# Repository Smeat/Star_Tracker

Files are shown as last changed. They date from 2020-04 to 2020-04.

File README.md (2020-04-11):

# Goals of this fork
 * Add support for esp32
 * Use an sdmmc driver and be able to use a larger library
   * SIMBAD library for Vmag <11 is about 16mb for the data and 30mb for the names
 * Use a nokia 5110 LCD with red backlight LEDs
 * Visual representation on the screen
 * WiFi connection to KStars/Stellarium -> done with LX200
 * ESP32 support only for now (8bit support may return once the esp32 is running)
# Arduino Star Tracker

This project aims an **automatic control for telescopes**, is **based on Arduino** and is **low-cost**!

The control utilizes a calibration method and various settings which enable you to control **any type of mount** (not just equatorial and altazimuthal) pointed at any direction.

The **total cost** of upgrading your mount should be around **75 USD** (*SkyWatcher SynScan GOTO Upgrade for EQ3-2* costs around *460 USD*).

## Features

See [future work](#future-work) for missing features (like communication via USB or Bluetooth). Some implemented and working freatures:

* **Manual control** with various precision (degrees, arc minutes and arc seconds).
* **Automatic pointing** at predefined coordinates.
* Onboard **catalogue of deep sky objects** (the one which is present in Stellarium), so you can search thousands of Messier, Caldwell and NGC objects.
* Precise **tracking** (for any type of mount).
* **Parking** to default position.
* **Calibration** of **mount pole** which works similarly to All-Star polar alignement.
* **Camera control** which alows you to take photos with predefined exposure time and with a predefined period.
* **Wireless control** via IR remote control.
* Real **asynchronous** control of **stepper motors** (any other code can be run in parallel). 
* **LX200** support

## Hardware setup

#### 0. What you will need:
* **Arduino MEGA2560**, unfortunately Arduino Uno cannot be used due to the lack of memory
* **Power supply** or battery, e.g. *12V* and around *2.5A* (depends on your stepper motors)
* *2×* **NEMA 17** stepper motor (forget about 28BYJ!)
* *2×* stepper motor driver like **A4988**
* *2×* stepper driver **extender for A4988** (we will modify this part, so you should consider custom design with 100μF capacitor)
* *4×* **4k7** or **10k resistor** (or any other suitable resistor you hold in your hands)
* *(optionally)* **Gearboxes** for the motors (battery screwdriver is typically much cheaper than profi gearboxes and has some planetary gearboxes inside!)
* *2×* **flexible shaft couplers** for joing the motors with mount
* **Real Time Clock**, note that *DS3231* or more precise clocks are preffered over DS1307 
* **microSD Card module**
* **16×2 LCD** (without I2C module)
* **10k Potentiometer**
* **IR receiver**
* **Remote control**, you can use your favourite one you use for TV or you can use any other for makers! This repo settings match with a [remote control](https://www.makeblock.com/project/me-ir-remote-controller) by Makeblock. 
* Some kind of **transistor**, e. g. *BC337* and suitable resistor, e. g. *1k ohms* 
* **Bunch of wires and connectors**

#### 1. Parts modification and tuning

You should **add** the four **resistors** between `STEP`-`GND` and `DIR`-`GND` pins **to avoid a jitter** of stepper motors at startup. 

A typical extender for A4988 has an `ENABLE` pin, however, we do not need it. Instead, we **need a pin for controlling microstepping**. That is why you should hardwire the three microstepping pins and you should add a single pin to control them. Search for *microstepping resolution truth table* of A4988.

A **cheap IR remote control** might have a **weak diode**. In that case, you won't be able to control the mount from a distant places. So I recommend you to **replace the diode with a better one.**  

You also need to **tune potentiometers of stepper drivers**. Search for *How to set output current limit on A4988 stepper driver*. This can reduce noise produced by the motors or you can remove **problems with skipping of steps**. 

Use the **potentiometer** connected to the LCD to **adjust contrast**.

#### 2. Wiring

Wiring diagram

## Software Settings & Uploding to Arduino

#### 0. Prepearing libraries

The following list contains libraries you will need to sucessfuly compile the Star Tracker project (most of them is included in the Arduino IDE by default):

* [RTCLib](https://github.com/adafruit/RTClib)
* [LiquidCrystal](https://github.com/arduino-libraries/LiquidCrystal)
* [SD](https://github.com/arduino-libraries/SD)
* [SPI](https://www.arduino.cc/en/Reference/SPI)
* [Wire](https://www.arduino.cc/en/Reference/Wire)
* [EEPROM](https://www.arduino.cc/en/Reference/EEPROM)

At first, **make sure you have already installed all the libraries**.

#### 1. General configuration

Next, you should **modify** the `src/config.h` file to fit your needs. Familiarize yourself with all the definitions in the file. You should **definitely change** `LONGITUDE`, `LATITUDE`, `REDUCTION_RATIO_xx` and `DEG_PER_MOUNT_REV_xx` variables! You also need to change `DEFAULT_POLE_xx` if you use an altazimuthal mount.

You may encounter a problem with **stucked motors**. In that case, I advice you to **adjust** `ACCEL_STEPS_xx`, `ACCEL_DELAY_xx`, `FAST_DELAY_START_xx` and `FAST_DELAY_END_xx`. Change these definitions in order to change motors speed or ac/deceleration.

#### 2. Remote control

You need to **change definitions of key codes** to fit the protocol used by your favourite remote control. Take look **at the beginning** of the `src/keypad.h` file. There are few definitions of `KP_KEY_xx` where `xx` describes the particular key. To figure out **codes used by your remote control**, upload the following sketch to your Arduino:

```
#include <Arduino.h>
#include <IRremote.h>
#include "src/config.h"

IRrecv ir(KEYPAD_IR_PIN);
decode_results results;

void setup(){
    Serial.begin(9600);
    ir.enableIRIn();
}

void loop(){
    if (!ir.decode(&results)) {
      delay(5);
      return;
    }
    Serial.println(results.value, HEX);
    ir.resume();
    delay(500);
}
```

Then **open the Serial monitor** and **observe the key codes** of pressed keys. Note that you will receive `0xFFFFFFFF` when you hold a key continuously.

You can also **change mapping of these keys to particular actions** in the `src/control.h` file (but be careful as these keys and actions should not cause conflicts and ambiguity).

#### 3. SD card and catalogue

Take an **empty and formatted microSD** card and **copy there the content** of the `SD` directory. It should be a single file `catalog.csv` which is a limited version of **Stellarium catalogue of deep space objects**. You can delete or add object to this file, however the structure and meaning of columns should be preserved.

#### 4. Real Time Clock

The `src/rtc_ds3231.h` file contains implementation of `Clock` class for `DS3231` module. In case you use **other module** or you want to obtain time from NTP servers, **implement** the `Clock` interface and change some lines in `Star_Tracker.ino`.

#### 5. Camera trigger

Similarly, you may need to change the implementation of the camera trigger control. The `src/CanonEOS1000D.h` file contains implementation of `CameraController` class for *Canon EOS1000D*. If you have other camera with **other trigger logic**, you should **create a new implementation** of `CameraController` and change some lines at `Star_Tracker.ino`. Note that in this case, you may also need a different wiring!

## Notes on precision

The only loss of precision is caused by Arduino's floating point unit which cannot work with 64-bit floating point numbers. Especially while computing extremal values of some goniometric funcions (tangens and other functions which are reduced to computing tangens). These problems can occur while pointing to stars near celestial pole. The GoTo feature can miss few arc minutes and alignement can be imprecise in that case. However points with lower DEC values should be handled properly.  

The tracking with very badly aligned mount can also be imprecise after some time because the speeds of DEC and RA motors are computed just once at the start of the movement. Unfortunately these speeds does not have to be constant necessarily.

## Future work

- [ ] enable **serial communication** with *USB* and *Bluetooth*
- [ ]  better **speed** computation **while tracking**
- [ ]  compute **alignment analytically**

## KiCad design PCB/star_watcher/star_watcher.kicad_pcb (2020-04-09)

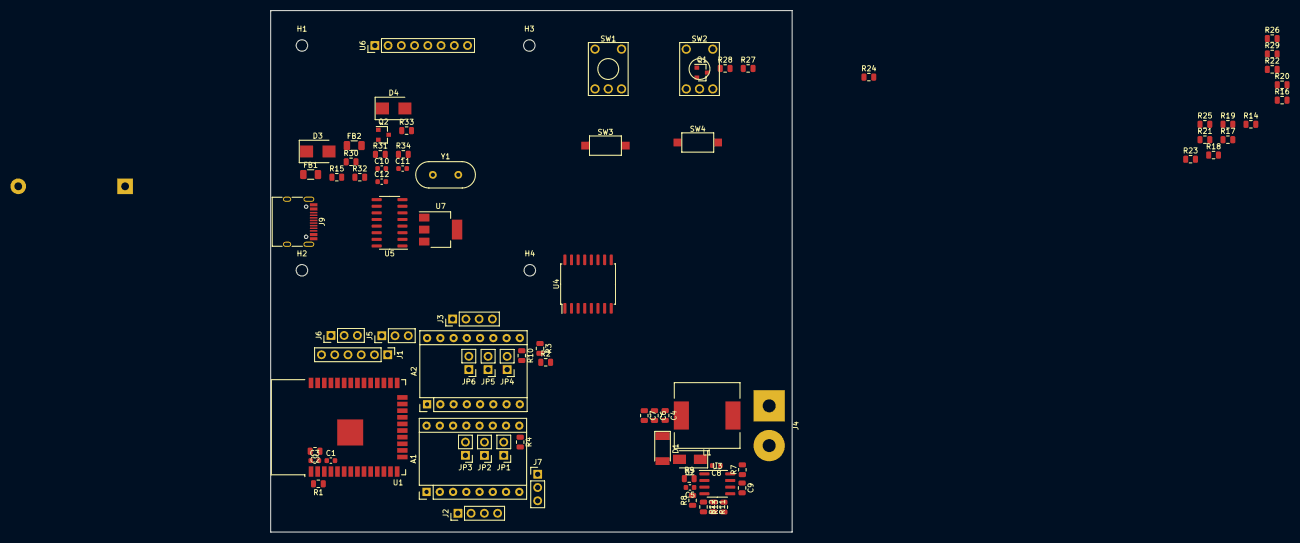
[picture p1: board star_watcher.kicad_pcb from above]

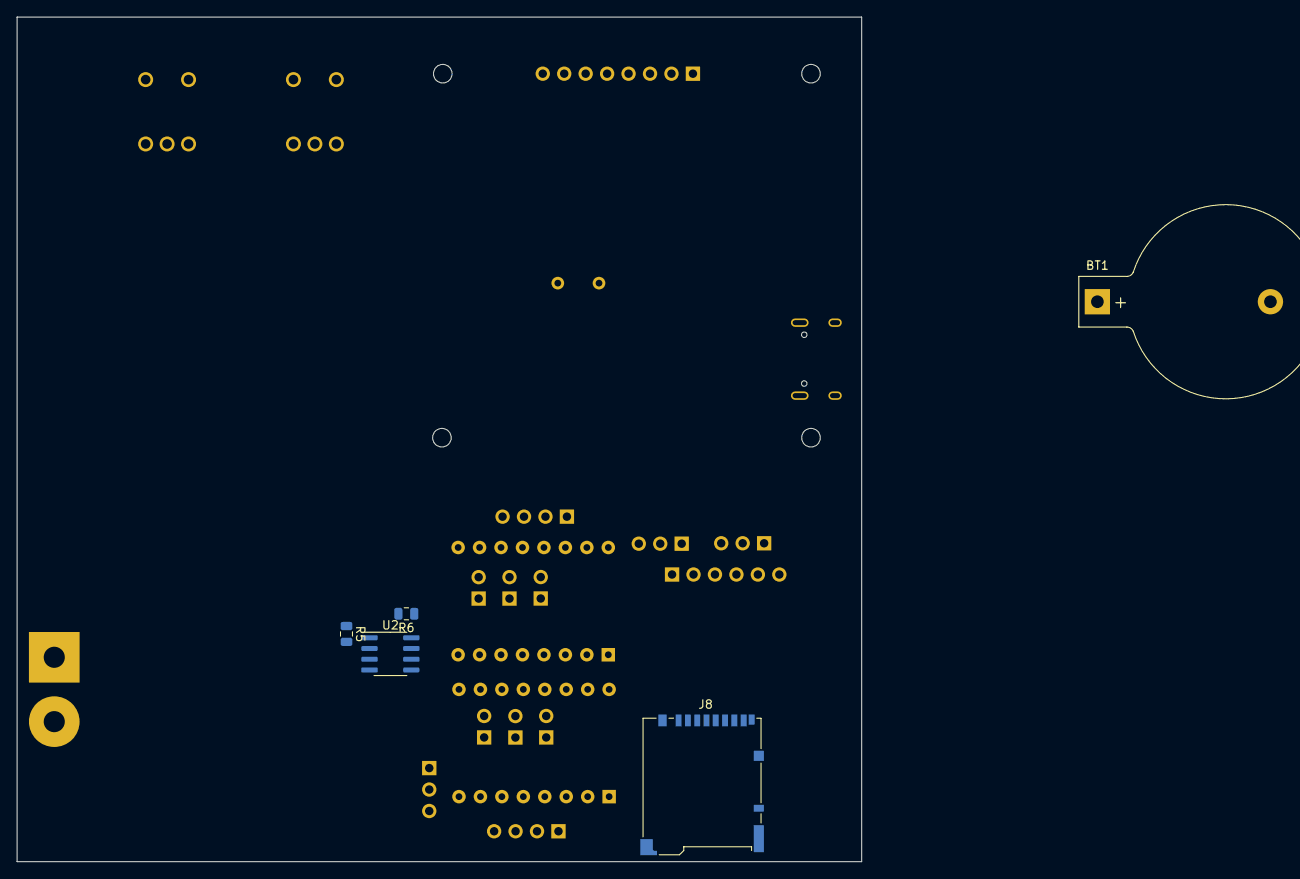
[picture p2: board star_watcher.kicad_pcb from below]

Board: 2 copper layers, 100.0 x 100.0 mm, 89 parts (5 on the bottom side), 78 nets, no tracks yet.

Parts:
A1, A2: Pololu_Breakout_A4988; Pololu_Breakout-16_15.2x20.3mm
BT1: Battery_Cell; BatteryHolder_Keystone_103_1x20mm
C1, C3, C8, C10: 0.1µF; C_0603_1608Metric
C2, C4, C6, C7, C9: 10µF; C_0805_2012Metric
C5: 150pF; C_0603_1608Metric
C11, C12: C; C_0603_1608Metric
D1: 3.5; D_MELF
D2: D_Schottky; D_SMA
D3, D4: D_TVS; D_SMB
FB1, FB2: Ferrite_Bead; L_1206_3216Metric
H1, H2, H3, H4: MountingHole; MountingHole_2.2mm_M2
J1: Programming; PinHeader_1x06_P2.54mm_Vertical
J2: Motor2; PinHeader_1x04_P2.54mm_Vertical
J3: Motor1; PinHeader_1x04_P2.54mm_Vertical
J4: input power; SolderWirePad_1x02_P7.62mm_Drill2.5mm
J5: UART1; PinHeader_1x03_P2.54mm_Vertical
J6: UART2; PinHeader_1x03_P2.54mm_Vertical
J7: I2C; PinHeader_1x03_P2.54mm_Vertical
J8: Micro_SD_Card_Det; microSD_HC_Hirose_DM3BT-DSF-PEJS
J9: USB_C_Receptacle_USB2.0; USB_C_Receptacle_HRO_TYPE-C-31-M-12
JP1, JP2, JP3, JP4, JP5, JP6: Jumper; PinHeader_1x02_P2.54mm_Vertical
L1: 22µH; L_12x12mm_H6mm
Q1, Q2: Q_PMOS_DGS; SOT-23
R1, R3, R4, R5, R6, R17, R18, R19, R20, R21, R22, R23, R24, R25, R26, R27, R28, R29: 10k; R_0805_2012Metric
R2: 240k; R_0805_2012Metric
R7, R8, R10: 100k; R_0805_2012Metric
R9: 59k; R_0805_2012Metric
R11, R14, R15, R16, R30, R31, R32, R33, R34: R; R_0805_2012Metric
R12: 40.2k; R_0805_2012Metric
R13: 200k; R_0805_2012Metric
SW1, SW2: Rotary_Encoder_Switch; KSA_Tactile_SPST
SW3, SW4: SW_Push; SW_SPST_CK_RS282G05A3
U1: ESP32-WROOM-32U; ESP32-WROOM-32
U2: DS3231MZ; SOIC-8_3.9x4.9mm_P1.27mm
U3: MP1584; SOIC-8_3.9x4.9mm_P1.27mm
U4: PCF8574; SOIC-16W_7.5x10.3mm_P1.27mm
U5: CH340G; SOIC-16_3.9x9.9mm_P1.27mm
U6: 5110; PinHeader_1x08_P2.54mm_Vertical
U7: AMS1117; SOT-223
Y1: 12MHz; Crystal_HC49-4H_Vertical

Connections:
+3V3: A1.2, A2.2, C2.1, C3.2, C4.2, C6.2, C7.2, D1.1, J1.2, J8.4, JP1.1, JP2.1, JP3.1, JP4.1, JP5.1, JP6.1, L1.2, Q1.3, Q2.3, R1.2, R4.2, R5.1, R6.1, R10.2, R11.2, R14.1, R17.1, R18.1, R19.1, R20.1, R21.1, R22.1, R23.2, R24.2, R25.1, R26.1, R27.1, R28.1, R29.1, U1.2, U2.2, U4.16, U5.4, U5.16, U6.6
+28V: A1.8, A2.8, C9.1, J4.1, Q2.2, R2.2, R7.1, R34.1, U3.7
/3.3V_USB: Q2.1, R32.1, U7.2, U7.4
/CE_5110: U1.27, U6.2
/DC_5110: U1.29, U6.3
/DIR1: A2.16, U1.28
/DIR2: A1.16, U1.31
/DTR: J1.3, SW4.1, U1.25, U5.13
/EN1: A2.9, R10.1
/EN2: A1.9, R4.1
/LCD_BACKLIGHT: Q1.2, U1.11
/PUSH1: R14.2, SW3.1, U1.5
/ROTARY1_A: R24.1, SW1.5, U4.7
/ROTARY1_B: R26.2, SW1.3, U4.9
/ROTARY1_PUSH: R27.2, SW1.1, U4.5
/ROTARY2_A: R23.1, SW2.5, U4.6
/ROTARY2_B: R25.2, SW2.3, U4.10
/ROTARY2_PUSH: R28.2, SW2.1, U4.4
/RST_5110: R29.2, U4.11, U6.1
/RTC_RST: U2.4, U4.12
/RTS: C1.1, J1.4, R1.1, U1.3, U5.14
/RX0: J1.5, U1.34, U5.2
/RX1: J5.2, U1.7
/RX2: J6.2, U1.6
/SCL: J7.2, R6.2, U1.37, U2.8, U4.14
/SDA: J7.1, R5.2, U1.36, U2.7, U4.15
/SD_CLK: J8.5, R21.2, U1.13
/SD_CMD: J8.3, R22.2, U1.23
/SD_D0: J8.7, R17.2, U1.24
/SD_D1: J8.8, R18.2, U1.26
/SD_D2: J8.1, R20.2, U1.14
/SD_D3: J8.2, R19.2, U1.16
/SPI_MOSI: U1.9, U6.4
/SPI_SCK: U1.8, U6.5
/STEP1: A2.15, U1.30
/STEP2: A1.15, U1.33
/TX0: J1.6, U1.35, U5.3
/TX1: J5.1, U1.10
/TX2: J6.1, U1.12
/USB_D+: D3.1, J9.A6, J9.B6, U5.5
/USB_D-: D4.2, J9.A7, J9.B7, U5.6
/VBUS: FB2.1, U7.3
/V_BAT_SENSE: R2.1, R3.2, U1.4
GND: A1.1, A1.7, A2.1, A2.7, BT1.2, C1.2, C2.2, C3.1, C4.1, C6.1, C7.1, C9.2, C10.1, C11.2, C12.2, D1.2, D2.2, D3.2, D4.1, FB1.2, J1.1, J4.2, J5.3, J6.3, J7.3, J8.6, J8.11, R3.1, R8.1, R9.1, R12.2, R13.1, R15.2, R30.1, R31.1, R33.2, R34.2, SW1.2, SW1.4, SW2.2, SW2.4, SW3.2, SW4.2, U1.1, U1.15, U1.38, U1.39, U2.5, U3.5, U4.1, U4.2, U4.3, U4.8, U5.1, U6.8
unnamed: A1.3, J2.1
unnamed: A1.4, J2.2
unnamed: A1.5, J2.3
unnamed: A1.6, J2.4
unnamed: A1.10, JP1.2
unnamed: A1.11, JP2.2
unnamed: A1.12, JP3.2
unnamed: A1.13, A1.14
unnamed: A2.3, J3.1
unnamed: A2.4, J3.2
unnamed: A2.5, J3.3
unnamed: A2.6, J3.4
unnamed: A2.10, JP4.2
unnamed: A2.11, JP5.2
unnamed: A2.12, JP6.2
unnamed: A2.13, A2.14
unnamed: BT1.1, U2.6
unnamed: C5.1, U3.3
unnamed: C5.2, R8.2
unnamed: C8.1, U3.8
unnamed: C8.2, D2.1, L1.1, U3.1
unnamed: C10.2, J9.S1, R15.1
unnamed: C11.1, U5.7, Y1.1
unnamed: C12.1, U5.8, Y1.2
unnamed: FB1.1, J9.A1, J9.A12, J9.B1, J9.B12
unnamed: FB2.2, J9.A4, J9.A9, J9.B4, J9.B9
unnamed: J9.A5, R30.2
unnamed: J9.B5, R31.2
unnamed: Q1.1, R16.2
unnamed: R7.2, R9.2, U3.2
unnamed: R11.1, R12.1, U3.4
unnamed: R13.2, U3.6
unnamed: R16.1, U6.7
unnamed: R32.2, R33.1, U7.1

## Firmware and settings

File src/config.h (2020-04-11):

#ifndef CONFIG_H
#define CONFIG_H

/* ================================== GENERAL SETTINGS ================================== */

#define SERIAL_BAUD_RATE       115200
#define EEPROM_ADDR            0            // starting EEPROM offset, 18 bytes needed 
#define VERSION                1.0

#define LONGITUDE              16.2607719   // CHANGE THIS !!!!!
#define LATITUDE               49.8225003   // CHANGE THIS !!!!!


/* ======================================== MOUNT ======================================= */

#define REDUCTION_RATIO_DEC     1              // reduction ratio of DEC motor gearbox (1:8)
#define REDUCTION_RATIO_RA      1              // reduction ratio of RA motor gearbox (1:8)
#define DEG_PER_MOUNT_REV_DEC   1 // reduction ratio of DEC mount gears (1:67)
#define DEG_PER_MOUNT_REV_RA    1  // reduction ratio of DEC mount gears (1:134)

#define DIRECTION_DEC           0    // 1 or 0 to swap DEC movement direction
#define DIRECTION_RA            0    // 1 or 0 to swap RA movement direction

#define DEFAULT_POLE_RA         0    // default equatorial coordinates of the mount pole 
#define DEFAULT_POLE_DEC        5   // these values are changed during alignment
#define DEFUALT_RA_OFFSET       0    // offset of RA axis (defines where mount's local RA is 0)


// Alignement is done by optimization of rotation matrix parameters (three), this is done 
// by a simple evolutionary strategy. Exact numeric solutions can be unstable due to Arduino
// doubleing point precision and I haven't found a better soluiton than this :( 

#define CAL_BUFFER_SIZE         12         // maximal number of point pairs used for alignmenet
#define OPT_PRECISION           5000000    // if objective is less then 1/OPT_PRECISION, opt. stops
#define OPT_POPULATION_SIZE     4          // population size of the ES
#define OPT_GENERAITONS         1250       // # gen., reduce for faster but less precise solutions
                                           // higher number of generations probably does not imply
                                           // better solutions
#define OPT_SIGMA               1.0        // initial sigma value
#define OPT_SIGMA_DECAY         0.997      // every generation is sigma multiplied by this value 


/* ==================================== STEPPER MOTORS ================================== */

#ifdef BOARD_ATMEGA
#define MOTORS_PORT             PORTK  // port of pins of stepper motors (serach for A. Mega pinout)
#define MOTORS_DDR              DDRK   // DDR of pins of stepper motors
#define STEP_PIN_DEC            PK2    // = A8 
#define DIR_PIN_DEC             PK1    // = A9
#define MS_PIN_DEC              PK0    // = A10
#define STEP_PIN_RA             PK5    // = A13
#define DIR_PIN_RA              PK4    // = A12
#define MS_PIN_RA               PK3    // = A11
#else
#define STEP_PIN_DEC            21    // = A8 
#define DIR_PIN_DEC             17    // = A9
#define MS_PIN_DEC              13    // = A10
#define STEP_PIN_RA             14    // = A13
#define DIR_PIN_RA              25    // = A12
#define MS_PIN_RA               22    // = A11
#endif

#define MICROSTEPPING_MUL       1   // level of microstepping (depends of your wiring of A4988 pins)

#define STEPS_PER_REV_DEC       (16*200)     // number of steps per DEC motor revolution (200 for NEMA 17)
#define STEPS_PER_REV_RA        (16*200)     // number of steps per RA motor revolution (200 for NEMA 17)

// period in µs
#define TMR_RESOLUTION  64

#define ACCEL_STEPS_DEC         256     // every ACCEL_STEPS_DEC steps is the delay in/decreased by
#define ACCEL_DELAY_DEC         64      // ACCEL_DELAY_DEC (should be even, multiple of 2)
#define FAST_DELAY_START_DEC    2048    // DEC delay at the start of fast movement (2048 us, ~488 Hz)
#define FAST_DELAY_END_DEC      0    // DEC delay at the end of fast movement (1024 us, ~976 Hz)

#define ACCEL_STEPS_RA          256     // every ACCEL_STEPS_RA steps is the delay in/decreased by
#define ACCEL_DELAY_RA          64      // ACCEL_DELAY_RA (should be even, multiple of 2)
#define FAST_DELAY_START_RA     2048    // RA delay at the start of fast movement (2048 us, ~488 Hz)
#define FAST_DELAY_END_RA       0    // RA delay at the end of fast movement (1024 us, ~976 Hz)

#define FAST_REVS_PER_SEC_DEC   1000000.0 / FAST_DELAY_START_DEC / STEPS_PER_REV_DEC 
#define FAST_REVS_PER_SEC_RA    1000000.0 / FAST_DELAY_START_RA  / STEPS_PER_REV_RA


/* ==================================== OTHER SETTINGS ================================== */

#define TRIGGER_PIN             40      // pin which controls camera trigger
#define SNAP_DELAY_MS           2000    // minimal delay (ms) between two snaps (camera protection)

#define SD_CS                   53      // SD card chip select pin

#define KEYPAD_IR_PIN           7       // IR receiver signal pin 
#define SHORT_HOLD_TIME_MS      200     // minimal duration (ms) of a fast remote control key press
#define LONG_HOLD_TIME_MS       800     // minimal duration (ms) of a slow remote control key press

#define DSP_DATA_PIN4           2       // LCD data pins
#define DSP_DATA_PIN5           3
#define DSP_DATA_PIN6           4
#define DSP_DATA_PIN7           5
#define DSP_ANODE_PIN           8       // LCD pin for controling brightness
#define DSP_ENABLE_PIN          11      // LCD enable pin
#define DSP_REGISTER_SEL_PIN    12      // LCD register select pin

/* ======================================== DEBUG_OUTPUT ======================================= */

// #define DEBUG_OUTPUT
// #define DEBUG_OUTPUT_MOUNT
// #define DEBUG_OUTPUT_TIME
// #define DEBUG_OUTPUT_CONTROL
// #define DEBUG_OUTPUT_KEYS

#endif

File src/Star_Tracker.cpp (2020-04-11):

#include "esp_attr.h"
#include "freertos/portmacro.h"
#include "freertos/projdefs.h"
#define LOG_LOCAL_LEVEL ESP_LOG_VERBOSE
#include "config.h"
#include "control/control.h"
#include "control/LX200.h"

#include "core/motor_controller.h"
#include "core/mount_controller.h"

#include "core/camera_controller.h"
#include "core/canon_eos1000d.h"

#include "core/clock.h"
#include "core/rtc_ds3231.h"

#include "net/TCP.h"
#include "net/wireless.h"

#include <stdint.h>
#include <soc/timer_group_struct.h>
#include <soc/timer_group_reg.h>
#include <esp_task_wdt.h>

RtcDS3231 ds3231;
Clock& my_clock = ds3231;

CanonEOS1000D eos;
CameraController& camera = eos; 

MountController mount(MotorController::instance());

Control control(mount, camera, my_clock);

void watchdog_feed() {
  TIMERG0.wdt_wprotect = TIMG_WDT_WKEY_VALUE;
  TIMERG0.wdt_feed = 1;
  TIMERG0.wdt_wprotect = 0;
}

void watchdog_add_task() {
	esp_task_wdt_add(NULL);
}

void tcp_task(void* param) {
	while(42) {
  		control.update();
  		tcp_update(lx200_handle_message);
		//uint8_t buf[] = ":Sr 10:10:10#";
//		lx200_handle_message(buf, strlen((char*)buf));
//		mount.set_target_dec(5);
//		mount.set_target_ra(5);
		vTaskDelay(10/portTICK_PERIOD_MS);
	}
}

void IRAM_ATTR motor_task(void* param) {
//	watchdog_add_task();
	uint8_t state = 0;
	while(42) {
		ulTaskNotifyTake(pdTRUE, portMAX_DELAY);
		digitalWrite(33, state);
		state = !state;
		MotorController::instance().trigger();
//		watchdog_feed();
	}
}

hw_timer_t* motor_timer = NULL;
static TaskHandle_t motor_task_handle = NULL;

void IRAM_ATTR motor_isr() {
	BaseType_t xHigherPriorityTaskWoken = pdFALSE;
	vTaskNotifyGiveFromISR(motor_task_handle, &xHigherPriorityTaskWoken);
	if(xHigherPriorityTaskWoken) {
		portYIELD_FROM_ISR();
	}
}

void info_task(void*) {
	while(42) {
//		mount.get_global_mount_orientation();

		log_v("Moving to 90,0");
		mount.move_absolute(90, 0);
		log_v("done!");
		// FIXME: timing problem. if delay is too small I don't reach the target
		// seems to be another problem
		do {
			log_v("Waiting for mount controller...");
			vTaskDelay(10000/portTICK_PERIOD_MS);
		} while(mount.is_moving());
		log_v("Moving to -20,0");
		mount.move_absolute(-20, 0);
		do {
			log_v("Waiting for mount controller...");
			vTaskDelay(10000/portTICK_PERIOD_MS);
		} while(mount.is_moving());
	}
}

void setup() {
	pinMode(33, OUTPUT);
  Serial.begin(SERIAL_BAUD_RATE);
  esp_log_level_set("*", ESP_LOG_VERBOSE);
  Serial.println("Starting tcp, lx200 and wifi");
  log_e("TEST!");
  ESP_LOGI("HI", "ESP test!");
  lx200_init(&mount, &my_clock);
  initWifiAP();
  tcp_init();
  delay(10);
  control.initialize();
  delay(100);

  xTaskCreatePinnedToCore(&tcp_task, "tcp_task", 18096, NULL, 5, NULL, 1);
//  xTaskCreatePinnedToCore(&info_task, "info_task", 8096, NULL, 5, NULL, 1);
  xTaskCreatePinnedToCore(&motor_task, "motor_task", 8096, NULL, 5, &motor_task_handle, 0);

  motor_timer = timerBegin(0, 80, true);
  timerAttachInterrupt(motor_timer, &motor_isr, true);
  timerAlarmWrite(motor_timer, TMR_RESOLUTION, true);
  timerAlarmEnable(motor_timer);

}

void loop() {
	mount.update_tracking();
	vTaskDelay(10/portTICK_PERIOD_MS);
//	watchdog_feed();
}

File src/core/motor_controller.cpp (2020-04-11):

#include "config.h"
#include "esp32-hal-gpio.h"
#include "freertos/portmacro.h"
#include "stdint.h"
#define FROM_LIB

#include <Arduino.h>
#include "esp32-hal-timer.h"
#include "motor_controller.h"

void MotorController::initialize() {
#ifdef BOARD_ATMEGA    
    uint8_t pin_mask = (1 << STEP_PIN_DEC) | (1 << DIR_PIN_DEC) | (1 << MS_PIN_DEC) |
                       (1 << STEP_PIN_RA)  | (1 << DIR_PIN_RA)  | (1 << MS_PIN_RA);

    MOTORS_DDR |= pin_mask;
    MOTORS_PORT &= ~pin_mask;

    #ifdef DEBUG_OUTPUT
        Serial.println(F("Stepper motors pins initialized:"));
        Serial.print(F("  Pinout: ")); Serial.println(pin_mask, BIN);
        Serial.print(F("  DDR:    ")); Serial.println(MOTORS_DDR, BIN);
        Serial.print(F("  PORT:   ")); Serial.println(MOTORS_PORT, BIN);
    #endif

    // Timer/Counter Control Register: set Fast PWM mode
    TCCR5A = 0x23 ; // || set mode 7 (Fast PWM) with
    TCCR5B = 0x09 ; // || prescaler 1 (no prescaling)

    // Output Compare Register: set interrupt frequency
    OCR5A = TIMER_TOP - 1;
    OCR5B = 0;
      
    // Timer/Counter Interrupt Mask Register: set interrupt TIMERx_COMPA_vect
    TIMSK5 |= (1 << OCIE5A);

    #ifdef DEBUG_OUTPUT
        Serial.println(F("TimerX initialized."));
        Serial.print(F("  TCCRxA: ")); Serial.println(TCCR5A, BIN);
        Serial.print(F("  TCCRxB: ")); Serial.println(TCCR5B, BIN);
        Serial.print(F("  TIMSKx: ")); Serial.println(TIMSK5, BIN);
    #endif
#else
	pinMode(STEP_PIN_DEC, OUTPUT);
	pinMode(DIR_PIN_DEC, OUTPUT);
	pinMode(MS_PIN_DEC, OUTPUT);
	pinMode(STEP_PIN_RA, OUTPUT);
	pinMode(DIR_PIN_RA, OUTPUT);
	pinMode(MS_PIN_RA, OUTPUT);

#endif

    _commands = queue<command_t>(8);

    _dec_balance = 0;
    _ra_balance = 0;
	_motor_lock = xSemaphoreCreateMutex();
}

void MotorController::stop() {

	xSemaphoreTake(_motor_lock, portMAX_DELAY);
    #ifdef DEBUG_OUTPUT
        Serial.println(F("Stopping both motors:"));
    #endif
    
    cli();
    _dec.pulses_remaining = 0;
    _ra.pulses_remaining = 0;
    sei();

    #ifdef DEBUG_OUTPUT
        Serial.print(F("  DEC: ")); Serial.println(_dec.pulses_remaining);
        Serial.print(F("  RA:  ")); Serial.println(_ra.pulses_remaining);
    #endif
      
#ifdef BOARD_ATMEGA
    MOTORS_PORT &= ~((1 << STEP_PIN_DEC) | (1 << STEP_PIN_RA)); // step pins to LOW

    #ifdef DEBUG_OUTPUT
        Serial.print(F("  PORT:   ")); Serial.println(MOTORS_PORT, BIN);
    #endif
#else
	digitalWrite(STEP_PIN_DEC, LOW);
	digitalWrite(STEP_PIN_RA, LOW);
#endif

    _commands.clear();
	xSemaphoreGive(_motor_lock);
}

double MotorController::estimate_fast_turn_time(double revs_dec, double revs_ra) {

    int sd, sr;
    revs_to_steps(&sd, &sr, revs_dec, revs_ra, false);
    
    auto time_dec = estimate_motor_fast_turn_time(sd, ACCEL_STEPS_DEC, ACCEL_DELAY_DEC, FAST_DELAY_START_DEC, FAST_DELAY_END_DEC);
    auto time_ra  = estimate_motor_fast_turn_time(sr, ACCEL_STEPS_RA,  ACCEL_DELAY_RA,  FAST_DELAY_START_RA,  FAST_DELAY_END_RA);

    return max(time_dec, time_ra);
} 

double MotorController::estimate_motor_fast_turn_time(double steps, int accel_each, int accel_amount, int delay_start, int delay_end) {

    double time = 0;

    double total_steps = floor(steps);
    double accel_steps = floor(steps);
    int delay_curr = delay_start; 

    for (accel_steps -= accel_each; (accel_steps > steps / 2.0) && (delay_curr > delay_end);) {
        time += (double)delay_curr * accel_each;
        delay_curr -= accel_amount;
        accel_steps -= accel_each;
    }
    accel_steps += accel_each;

    return (2 * time + (2 * accel_steps - total_steps) * delay_curr) / 1000.0; 
}

void MotorController::fast_turn(double revs_dec, double revs_ra, boolean queueing) {
    turn_internal({revs_dec, revs_ra, FAST_DELAY_START_DEC, FAST_DELAY_START_RA, FAST_DELAY_END_DEC, FAST_DELAY_END_RA, false}, queueing);
}

void MotorController::slow_turn(double revs_dec, double revs_ra, double speed_dec, double speed_ra, boolean queueing) {
    // revolutions per second convert to delay in micros
    // there might be some overflows, but nobody cares ... (hopefully)
    uint32_t delay_dec = 1000000.0 / (speed_dec * STEPS_PER_REV_DEC * MICROSTEPPING_MUL);
    uint32_t delay_ra  = 1000000.0 / (speed_ra  * STEPS_PER_REV_RA  * MICROSTEPPING_MUL);
    turn_internal({revs_dec, revs_ra, delay_dec, delay_ra, delay_dec, delay_ra, true}, queueing);
}

void MotorController::turn_internal(command_t cmd, bool queueing) {
    if (queueing && !is_ready()) {
        _commands.push(cmd);
        return;
    }
	xSemaphoreTake(_motor_lock, portMAX_DELAY);
    int steps_dec, steps_ra;
    revs_to_steps(&steps_dec, &steps_ra, cmd.revs_dec, cmd.revs_ra, cmd.microstepping);
	log_d("turning by DEC %f RA %f revs, %d %d steps %d %d balance",cmd.revs_dec, cmd.revs_ra, steps_dec, steps_ra, this->_dec_balance, this->_ra_balance);
	log_d("total steps ra %d dec %d", _dec_balance, _ra_balance);
	
    //cli();

    // wait 1ms for pins to stabilize if needed
    bool dec_rev = cmd.revs_dec < 0;
	bool ra_rev = cmd.revs_ra < 0;


    int32_t effective_steps_dec = steps_dec;
    int32_t effective_steps_ra = steps_ra;

    _dec.pulses_to_accel = 0;
    _ra.pulses_to_accel  = 0;

    _dec.steps_total = effective_steps_dec;
    _ra.steps_total = effective_steps_ra;
    
    _dec.target_steps_delay = cmd.delay_end_dec;
    _ra.target_steps_delay  = cmd.delay_end_ra;

    _dec.start_steps_delay = cmd.delay_start_dec;
    _ra.start_steps_delay  = cmd.delay_start_ra;

    step_micros(&_dec, effective_steps_dec * 2, _dec.start_steps_delay, dec_rev);
    step_micros(&_ra,  effective_steps_ra  * 2, _ra.start_steps_delay, ra_rev);
        log_d("Initializing new movement.");
        log_d("  revs DEC:       %f", cmd.revs_dec);
        log_d("  resv RA:        %f", cmd.revs_ra);
		log_d("  steps DEC: %d RA: %d", effective_steps_dec, effective_steps_ra);
        log_d("  micro s. (t/f): %s", cmd.microstepping ? "enabled" : "disabled");
		log_d("Direction dec %d ra %d", digitalRead(DIR_PIN_DEC), digitalRead(DIR_PIN_RA));
	xSemaphoreGive(_motor_lock);

    // compensate coarse resolution of the full-step movement
    if (!cmd.microstepping) {
        double revs_dec, revs_ra;
        steps_to_revs(&revs_dec, &revs_ra, steps_dec - effective_steps_dec, steps_ra - effective_steps_ra, false);
        slow_turn(revs_dec, revs_ra, FAST_REVS_PER_SEC_DEC / MICROSTEPPING_MUL, FAST_REVS_PER_SEC_RA / MICROSTEPPING_MUL, true);
    }

#ifdef BOARD_ATMEGA
    TCNT1 = 0; // reset Timer1 counter
#endif

    //sei();
}

bool MotorController::change_pin(byte pin, byte value) {
#ifdef BOARD_ATMEGA
    if (((MOTORS_PORT >> pin) & 1) == value) return false;
    MOTORS_PORT ^= (-value ^ MOTORS_PORT) & (1 << pin);
#else
	uint8_t state = digitalRead(pin);
	if(state == value) return false;
	digitalWrite(pin, value);
	log_d("Changed pin %d to %d", pin, value);
#endif
    return true;
}
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

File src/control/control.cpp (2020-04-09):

#define FROM_LIB

#include "control.h"

void Control::initialize() {

    load(_shooting_time_buffer, EEPROM_ADDR, 1, 9999, 30);
    load(_shooting_delay_buffer, EEPROM_ADDR + 2, 1, 9999, 30);
    load(_brightness_buffer, EEPROM_ADDR + 4, 0, 255, 128);

    _mount.initialize();
	log_i("Mount init done");
    _display.initialize(_brightness_buffer);
	log_i("display init done");

#ifdef BOARD_ATMEGA
    SD.begin(SD_CS);
    _sd = &SD;
#endif
    _keypad.initialize();
	log_i("keypad init done");
    _camera.initialize();
	log_i("camera init done");

    _clock.obtain_time();
	log_i("clock init done");

    delay(100);

    _state = MAIN;
    _state_changed = true;
}

void Control::update() {

    _keypad.update();
    _camera.update();

    _last_state_changed = _state_changed;
    _last_substate_changed = _substate_changed;
    _state_changed = false;
    _substate_changed = false;

    if (_keypad.pressed(C_EXIT)) change_state(HELP);

    switch (_state) {
        case MAIN: 	  main_menu(); break;
        case HELP: 	  help_menu(); break;
        case GOTO: 	  goto_menu(); break;
        case CALIB:   calibration_menu(); break;
        case SHOOT:   camera_menu(); break;
        case CATALOG: catalogue_menu(); break;
        case TIME:    time_menu(); break;
        case BRIGHT:    brightness_menu(); break;
        case POSITION:  position_menu(); break;
    }
}

void Control::help_menu() {

    if (_last_state_changed) _last_substate_change_time = millis();

    if (_keypad.pushed(C_EXIT)) change_state(MAIN);

    if ((millis() - _last_substate_change_time) > INFO_SCREEN_MS) {
        _last_substate_change_time = millis();
        change_substate(increment_substate());
        if (_substate > S9) change_substate(S0);
    }

    _display.render_help(_last_state_changed || _last_substate_changed, _substate);			
}

void Control::position_menu() {

    if (_keypad.pushed(C_EXIT)) change_state(MAIN);

    auto orientation = _mount.get_global_mount_orientation();
    _display.render_position(_last_state_changed || _last_substate_changed, orientation.ra, orientation.dec);			
}

void Control::brightness_menu() {

    if (_keypad.pushed(C_EXIT)) {
        change_state(MAIN);
        save(_brightness_buffer, EEPROM_ADDR + 4);
    }

    int change = 0;
    if (_keypad.pressed(C_ARROW_UP))    	change = 32;
    else if (_keypad.pressed(C_ARROW_DOWN)) change = -32;	
    else if (_keypad.pushed(C_ARROW_UP))    change = 8;
    else if (_keypad.pushed(C_ARROW_DOWN))  change = -8;

    _brightness_buffer += change;
    if (_brightness_buffer > 255) _brightness_buffer = 255;
    if (_brightness_buffer < 0) _brightness_buffer = 0;

    _display.render_brightness(_last_state_changed, _brightness_buffer, change != 0);
    _display.set_brightness(_brightness_buffer);
}

void Control::main_menu() {

    if (_keypad.pressed(C_TRACKING))     	_mount.set_tracking();
    else if (_keypad.pushed(C_GOTO))     	change_state(GOTO);
    else if (_keypad.pushed(C_POSITION)) 	change_state(POSITION);
    else if (_keypad.pushed(C_PARKING)) {
        _camera.reset();
        _mount.stop_all();
        _mount.set_parking();
    }
    else if (_keypad.pushed(C_BRIGHTNESS))  change_state(BRIGHT);	
    else if (_keypad.pushed(C_SHOOT))       _camera.shoot(_shooting_time_buffer, _shooting_delay_buffer);
    else if (_keypad.pressed(C_CALIBRATION)) {		
        double ra_offset;
        load(ra_offset, EEPROM_ADDR + 6, 0.0, 360.0, (double)DEFUALT_RA_OFFSET);

        MountController::coord_t pole;
        load(pole, EEPROM_ADDR + 10);
        if (isnan(pole.ra) || pole.ra < 0 || pole.ra >= 360) pole.ra = DEFAULT_POLE_RA;
        if (isnan(pole.dec) || pole.dec < -90 || pole.dec > 90) pole.dec = DEFAULT_POLE_DEC;

        _display.render_calibration_loaded(true, pole.ra, pole.dec, ra_offset);
        _mount.set_mount_pole(pole, ra_offset);

        delay(INFO_SCREEN_MS);
        _state_changed = true;
    }
    else if (_keypad.pushed(C_CALIBRATION)) change_state(CALIB);
    else if (_keypad.pushed(C_CAMERA)) 		change_state(SHOOT);
    else if (_keypad.pushed(C_TIME))   		change_state(TIME);
    else if (_keypad.pushed(C_MESSIER)) {
        change_state(CATALOG);
        change_substate(S0);
    }
    else if (_keypad.pushed(C_CALDWELL)) {
        change_state(CATALOG);
        change_substate(S1);
    } 
    else if (_keypad.pushed(C_NGC)) {
        change_state(CATALOG);
        change_substate(S2);
    }

    manual_control(S0, S1, S2, S3);

    _display.render_main(_last_state_changed || _last_substate_changed, _substate, Clock::get_LST(), 
                         _mount.is_tracking(), _mount.is_moving(), _camera.update());
            
    if (_keypad.pushed(C_EXIT)) {
        if (_camera.update()) _camera.reset();
        else if (_mount.is_tracking()) _mount.stop_tracking();
        else if (_mount.is_moving()) _mount.stop_all();
    } 
}

void Control::goto_menu() {

    if (_last_state_changed) {
        clear_position_buffers();
        _display.render_goto_info(true);
        delay(INFO_SCREEN_MS);
    }
    _display.render_goto(_last_substate_changed || _last_state_changed, _substate, _ra_buffer, _dec_buffer);
                
    if (_substate == S5 && _keypad.pushed(C_ENTER)) {

        change_state(MAIN);
        auto coords = position_buffers_to_coords();
        _mount.stop_all();
        _camera.reset();
        _mount.move_absolute(coords.dec, coords.ra);

        return;
    }

    if (_keypad.pushed(C_EXIT)) change_state(MAIN);
    if (_keypad.pushed(C_ENTER)) change_substate(increment_substate());

    int pushed_digit = get_pushed_digit();
    if (pushed_digit == -1) return;

    switch (_substate) {
        case S0: add_digit(_ra_buffer[0], pushed_digit, 0, 23); break;
        case S1: add_digit(_ra_buffer[1], pushed_digit, 0, 59); break;
        case S2: add_digit(_ra_buffer[2], pushed_digit, 0, 59); break;
        case S3: add_digit(_dec_buffer[0], pushed_digit, -89, 89); break;
        case S4: add_digit(_dec_buffer[1], pushed_digit, 0, 59); break;
        case S5: add_digit(_dec_buffer[2], pushed_digit, 0, 59); break;
        default: break;
    }
}
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

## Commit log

2020-04-06 Fix a bunch of warnings
    [control.cpp, control.h, motor_controller.cpp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]
2020-04-06 [WIP] Make it _compilable_ on esp32. _NOT FUNCTIONAL_
2020-04-07 Rename DEBUG defines to avoid collisions
    [config.h, control.cpp, motor_controller.cpp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]
2020-04-07 Fix esp32 compilation with debug enabled
    [motor_controller.cpp]
2020-04-09 Add tcp socket
2020-04-09 [WIP] Add pcb
    [star_watcher.kicad_pcb, star_watcher.sch]
2020-04-09 Way too large commit. Not crashing on esp32 now Add a target command to use with lx200
    [Star_Tracker.cpp, config.h, control.cpp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]
2020-04-10 Add support for getting the current target
2020-04-10 KStars seems to have RA and DEC switched? I am probably just too dumb
2020-04-10 Add a bunch of LX200 commands and fix old ones
    [Star_Tracker.cpp, config.h, mount_controller.cpp]
2020-04-10 Add 64µS interrupt for esp32
2020-04-10 Fix pin init on esp32
    [motor_controller.cpp]
2020-04-11 Working with smaller values Removes old atmega code Add pin toggle for debugging loop stability The direction is now a variable instead of using the pin as a variable
    [Star_Tracker.cpp, config.h, motor_controller.cpp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]
